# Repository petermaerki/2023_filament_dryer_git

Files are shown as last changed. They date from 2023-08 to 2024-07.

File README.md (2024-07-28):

# 2023_filament_dryer

This page is explains the physical aspects.

These topics are not covered:
* Open Hardware and Open Software...
* How to build
* User Guide
* How to run grafana etc.

## Introduction

This filament dryer is used to dry 3D printer filament.

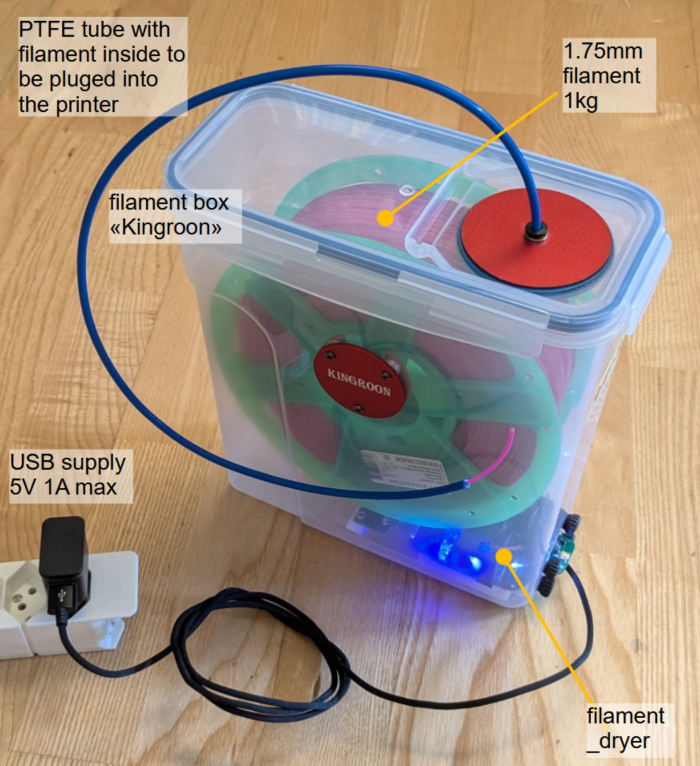
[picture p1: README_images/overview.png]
Overview


A plastic box (Aliexpress, Kingroon, USD23) is equiped with a dryer module. The module is pluged to USB power (5V, 1A max). The dryer contains about 10g of dried silicagel. A fan blows dry air around the filament. The silicagel will be automatically regenerated when saturated with water: its heated up and the wet air is blown to the enviroment.
It takes about 5 days to dry 1 kg of 1.75 mm filament.

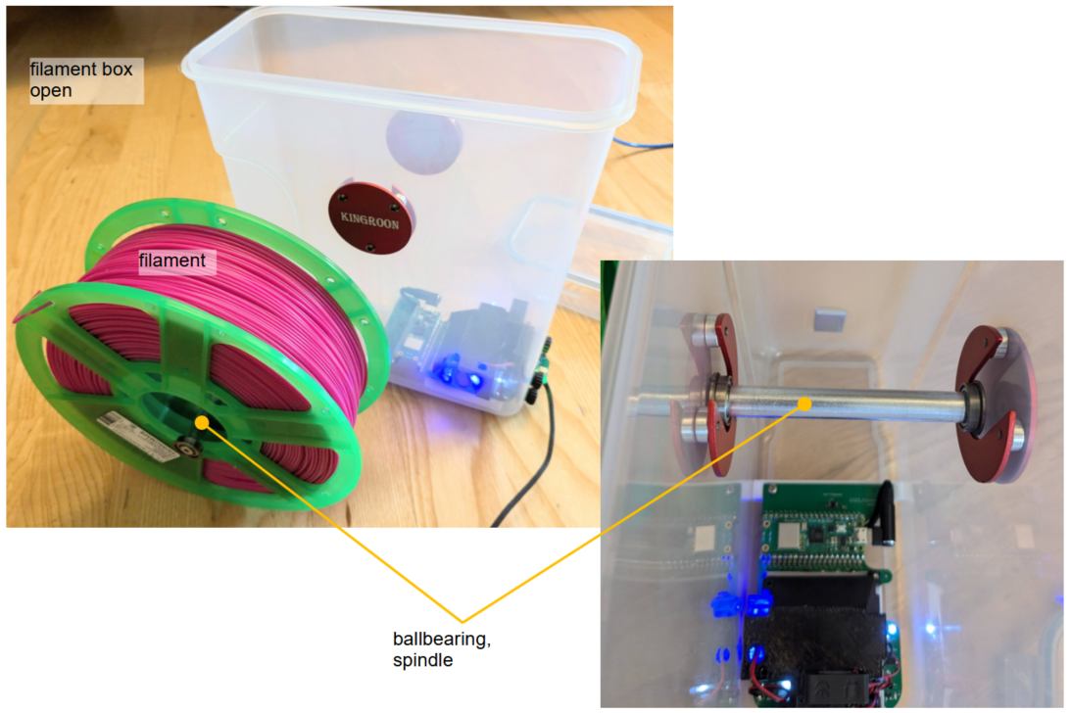
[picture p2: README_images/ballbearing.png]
Spindle


The filament roll is held by a spindle with ballbearings. 

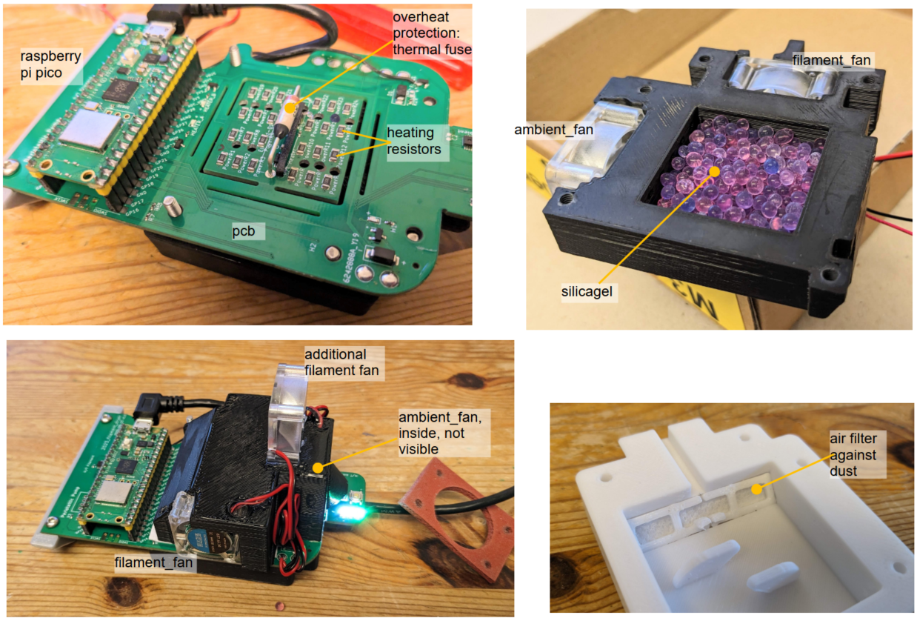
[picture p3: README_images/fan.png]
details


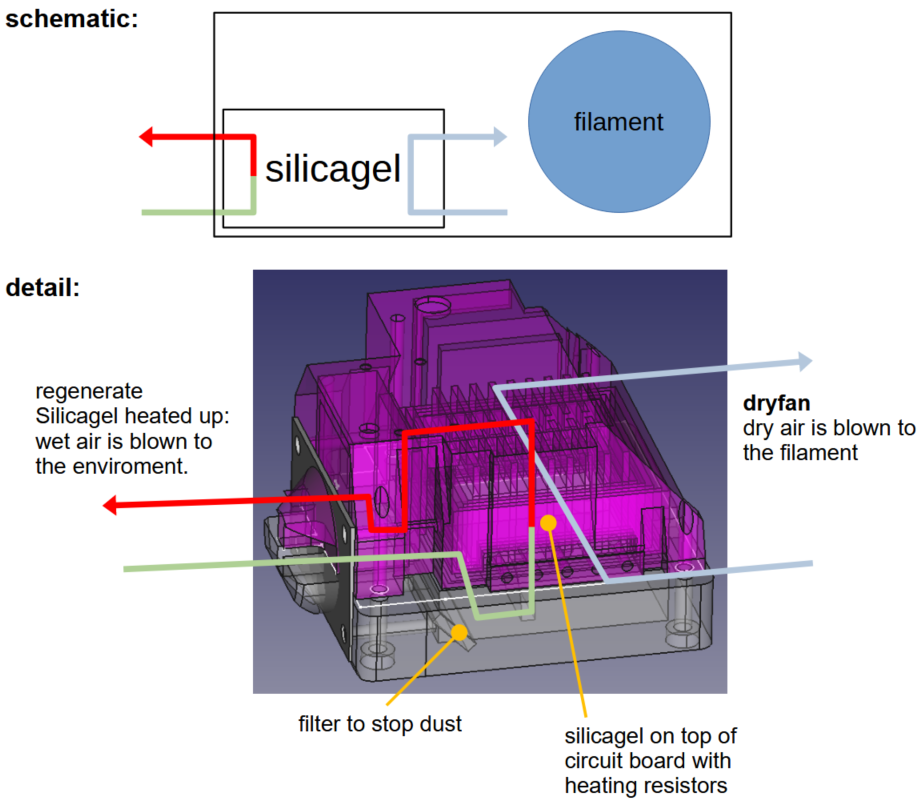
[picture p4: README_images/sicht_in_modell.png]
Airflow Model


## Drying process

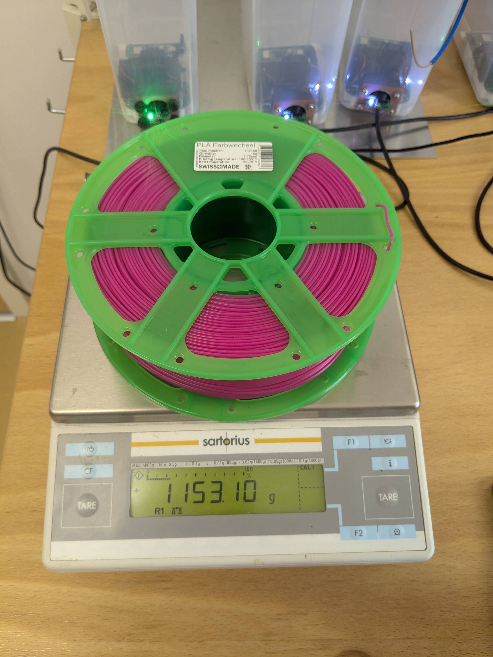
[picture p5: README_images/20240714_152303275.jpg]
Filament roll on the scale


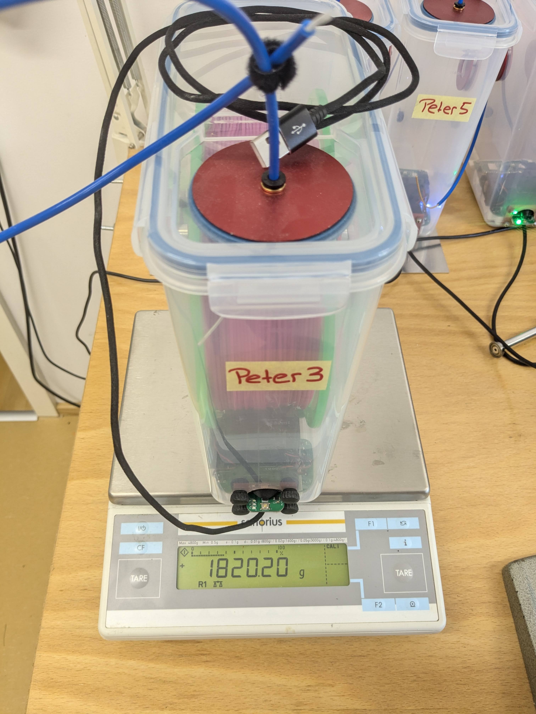
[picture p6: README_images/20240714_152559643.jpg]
Complete box an scale


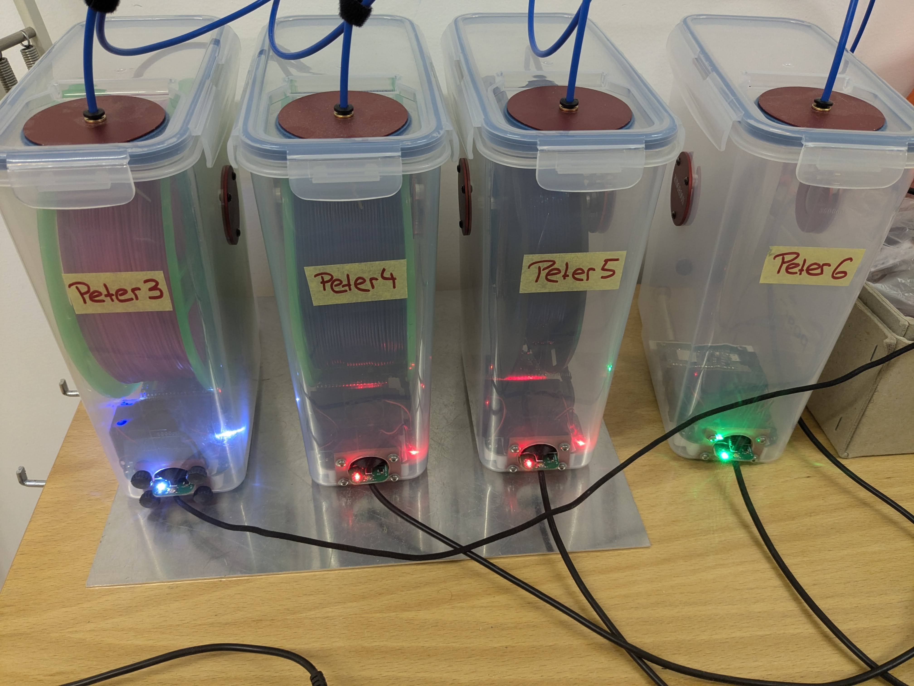
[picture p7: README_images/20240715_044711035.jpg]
Boxes


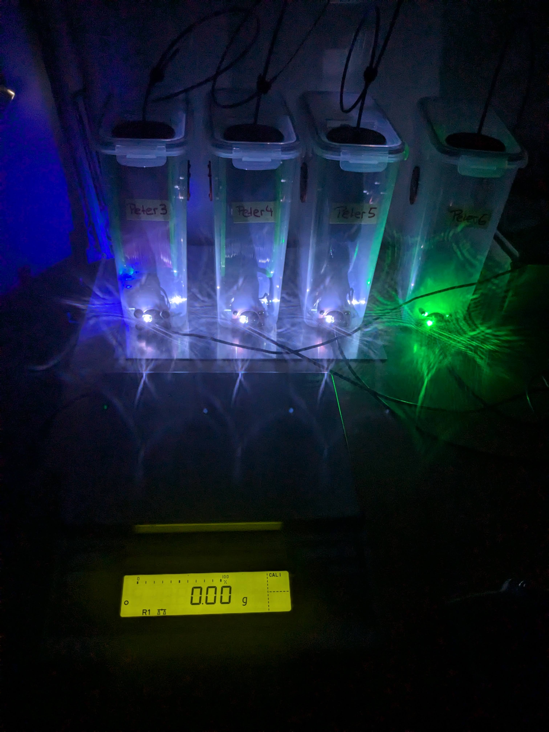
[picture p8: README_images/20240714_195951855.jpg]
Boxes in the dark


Three rolls of filament are placed in filament_dryers. PLA, PETG and TPU. The rolls have been laying around in my workshop for a long time and therefore I assume they are equally "wet". The filament_dryer is pluged in and I measure the weight of the hole dryer box over the next two weeks.
In the diagramm I show the weight reduction relative to the filament weight (1 kg for example).

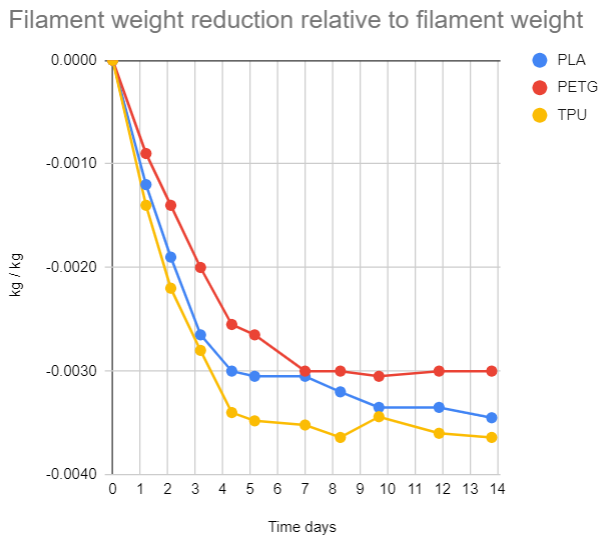
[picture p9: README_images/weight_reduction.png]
Weight loss against time


Filament types
* PLA	Pink	PLA 1.75 mm 102468 Purefil 1kg
* PETG	dunkelblau	PETG 1.75 mm 102478 Purefil 1 kg
* TPU	blau_transparent	TPU 1.75 mm LOT 20221216 Aliexpress 0.5 kg

### Conclusion

* All of the tested Filaments loose about 3 gramm water per kg filament over a week. I assume the water content after a week is low and perfect for printing.
* The fluctuation of the weight after day 6 is not a measuring error. It is due to the regeneration cycle of the dryer. Water goes into the dry box through the plastic walls or air gaps and gets out through the regenation cycle every few days.

### Drying details

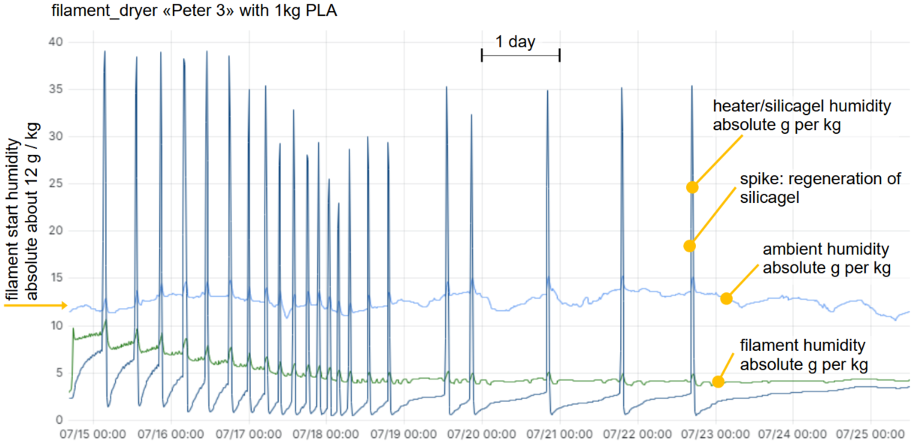
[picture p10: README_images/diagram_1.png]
Diagram two weeks absolute humidity

As an example the details of the drying over two weeks are shown.
I do show the absolute water content of the air in g per kg of air. 1 kg air corresponds to about 1 m3 air. The absolute humidity does not depend on temperature and after playing around with different himidity units for a long time, I decided to prefer this unit.

The humidity of the air around the filament changes from 12 g/kg at the start (the filament was laying around in my workshop at this himidity, ambient) to 4 g/kg after one week.

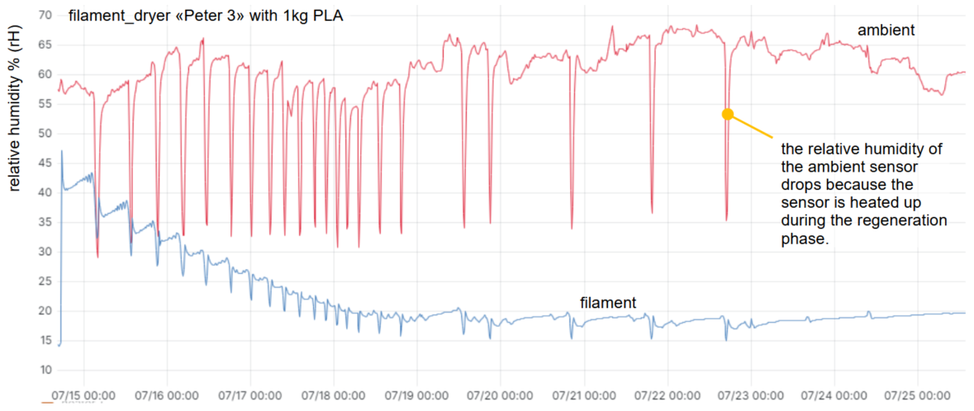
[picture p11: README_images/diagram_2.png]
Diagram two weeks relative humidity

The relative humidity in my workshop is in the range of 60%. The relative humidity of the air arount the filament is decreased down to below 20%.

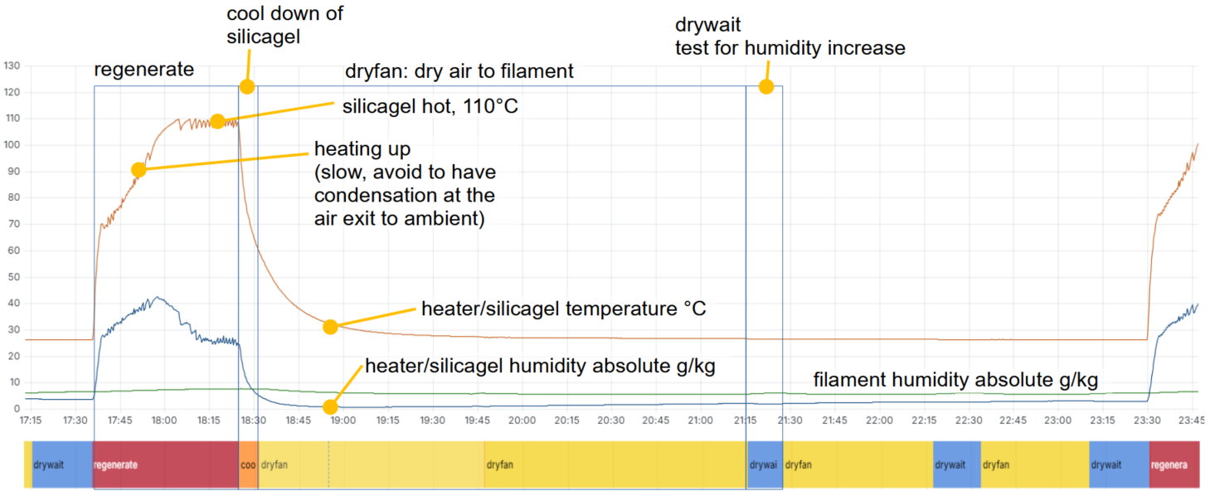
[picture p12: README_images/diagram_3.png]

One cycle of regeneration and drying.

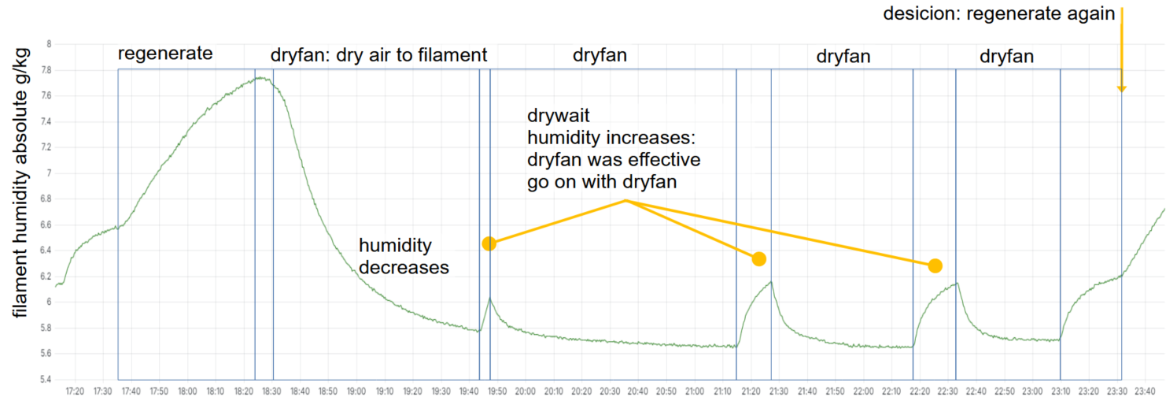
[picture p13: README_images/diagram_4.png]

The decision how to proceed is made due to changes of measurenents. If we only observe changes we are not sensitive to measurements errors/offsets. 

# Grafana
It is possible to log to grafana.
[Example](http://www.maerki.com:3000/goto/Yx-3weXSR?orgId=1)

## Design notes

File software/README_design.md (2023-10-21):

# Design decisions

## WLAN and MQTT internet connections

* At micropython boot:
  * Start watchdog
  * wlan connect
  * mqtt broker connect
  * If failed:
    * Just remember, do not try to connect/reconnect
    * Run statemachine and do not access WLAN
    * After 1h: reboot
  * If success:
    * Run statemachine and access WLAN
    * If socket error during mqtt publish:
      * Just remember, do not try to connect/reconnect
    * After 1h: reboot

## Statemachine and Watchdog

* Statemachine
  * Start in state `drywait`
  * Just before `sensors.measure()`: Reset watchdog.

# User elements

* Button long: Reboot (and reconnect to wlan)
* Button short: Next state
* LED green: state `drywait`
* LED white: state `dryfan` 
* LED red: state `regenerate/cooldown`

# WLAN in seperate thread

* No timer watchdog is required as the statemachine will feed() the wdt.

```
wdt_counter = 1
def feed():
  global wdt_counter
  if wdt_counter > 0:
     wdt_counter -= 1
  if wdt_counter == 0:
     wdt.feed()

Other core

def wlan_connect():
   wdt_counter = 10 # 10 times 8s
   wlan.connect()
   wdt_counter = 0
```
```
class SlowWdt:
  def __init__(self):
    self._start_ms: int = None
    self._expiration_ms: int = None

  def __activate__(self, expiration_ms: int):
    self._expiration_ms = expiration_ms
    self._start_ms = time.now()
  
  def feed(self):
    duration_ms = diff(time.now, self._start_ms) 
    if duration_ms > self._expiration_ms:
       reboot

def feed():
  global wdt_counter
  if wdt_counter > 0:
     wdt_counter -= 1
  if wdt_counter == 0:
     wdt.feed()

def wlan_connect():
  wdt_wlan_start_ms = time.now()
  wlan.connect()
  wdt_wlan_start_ms = None
```

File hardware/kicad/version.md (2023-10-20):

# 2023-07-16 v0.1

Manuelle Korrekturen
USB3 Muffe nach hinten verschoben
Um 90 Grad gedreht: U1, U4, U5, U6

# 2023-07-17 v0.2

Fix Footprint of R Heating
Add R for 1wire

Manuelle Korrekturen
USB3 Muffe nach hinten verschoben
Um 90 Grad gedreht: U1, U4, U5, U6

# 2023-07-18 v0.3

Final steps

* Schema Editor: File -> Page Settings: Update Revision & issue date
* Schema Editor: Inspect -> Electrical Rule Checker -> 0 Errors, 0 Warnings
* PCB Editor: File -> Page Settings: Update Revision & issue date
* PCB Editor: Tools -> Clean up tracks & vias -> check all
* PCB Editor: Inspect -> Design Rule Checker -> 0 Errors, 0 Warnings
* PCB Editor: Button "Fabrication Toolkit"

Manuelle Korrekturen in JLC
USB3 nach hinten verschoben
Um 90 Grad gedreht: U1, U4, U5, U6

# 2023-09-08 v0.6

Probleme:
 * FET Q1-Q8: Pins falsch.
 * FET Q1-Q8: Falsch: https://ngspice.sourceforge.io/docs/ngspice-manual.pdf
 * FET Q1-Q8: Korrekt: https://datasheet.lcsc.com/lcsc/1810010522_Infineon-Technologies-IRLML6244TRPBF_C143946.pdf
 * R1 4.7k: Zu gross, 2k ist ok.
 * Warum hat JLCPCB Komponenten verdreht?
 * Schrauben für Gehäuse: Sperrzone um Kurzschluss zu verhindern.
 * Schema: HT_SILICAGEL_SCA -> HT_SILICAGEL_SDA

 * Konsistente Namensgebung: SILICAGEL, FILAMENT, AMBIENT. Falsch ist BOARD, EXTs

# 2023-09-28 v1.0
  * DONE: GPIO_FAN_AMBIENT is missing!
  * DONE: HT Spare weg!
  * DONE: Ambient Sensor: C2 ist unter dem Gehäuse!
  * OK: Löcher unter Pico sind unnütz!
  * DONE: silicagel_fan -> filament_fan
  * DONE: Unterhalb Pico: Kein Kupfer wegen Antenne

# 2023-10-20 v1.1

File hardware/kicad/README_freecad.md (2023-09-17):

# FreeCAD

## PCB -> KiCad

### FreeCAD

In Python Console:

```python
objs=[]
objs.append(FreeCAD.getDocument("_0230917p_filament_dryer_silicagel").getObject("Body002"))
import importDXF
importDXF.export(objs, u"/tmp/dryer_board.dxf")

del objs
```

### KiCad

* KiCad PCB: Menu `File -> Import Graphics`
  * `/tmp/dryer_board.dxf`
  * At `0`, `0`
  * Layer `Edge.Cuts`
  * Import scale: `1`
  * `check` Group Items
  * Default line width `0.2 mm`
  * Default units: `Millimeters`

Flip horizontally!

## Footprint -> KiCad

### FreeCAD

In Python Console:

```python
objs=[]
objs.append(FreeCAD.getDocument("_0230917p_filament_dryer_silicagel").getObject("Body"))
import importDXF
importDXF.export(objs,u"/tmp/dryer_print3d.dxf")

del objs
```

In VSCode:

`mv /tmp/dryer_print3d.dxf ./hardware_kicad/Parts/dryer_print_3d`

### KiCad

Footprint Editor

* Menu `New Footprint...`
  * Name: `dryer_print3d`
  * Footprint type `Other`

* Menu `File -> Import Graphics`
  * `/tmp/dryer_print3d.dxf`
  * At `0`, `0`
  * Layer `F.Silkscreen`
  * Import scale: `1`
  * `check` Group Items
  * Default line width `0.2 mm`
  * Default units: `Millimeters`

## 3D Model -> KiCad

### FreeCAD

In Python Console:

```python
objs=[]
objs.append(FreeCAD.getDocument("_0230917p_filament_dryer_silicagel").getObject("Body"))
import ImportGui
ImportGui.export(objs,u"/tmp/dryer_print3d.step")

del objs
```

In VSCode:

`mv /tmp/dryer_print3d.step ./hardware_kicad/Parts/dryer_print_3d`

### KiCad

* Edit Footprint Properties
* Add 3D Model
* Rotation Y: `180`

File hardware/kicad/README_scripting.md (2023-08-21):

https://dev-docs.kicad.org/en/python/pcbnew/

https://github.com/mcbridejc/kicad_component_layout/blob/master/examples/led-circle/layout.py

--------------
```python

import pcbnew; print(pcbnew.PLUGIN_DIRECTORIES_SEARCH)
/usr/share/kicad/scripting
/usr/share/kicad/scripting/plugins
/home/maerki/.config/kicad/7.0/scripting
/home/maerki/.config/kicad/7.0/scripting/plugins
/home/maerki/.local/share/kicad/7.0/scripting
/home/maerki/.local/share/kicad/7.0/scripting/plugins
/home/maerki/.local/share/kicad/7.0/3rdparty/plugins

import pcbnew
ap = pcbnew.ActionPlugin()

pcb = pcbnew.GetBoard()

footprints = pcb.GetFootprints()
for footprint in footprints: print(footprint)

refdes = ""
mod = pcb.FindFootprintByReference(refdes)

footprint.GetPath().AsString()
'/85b4834f-1429-4c28-a1bb-14cdbf0ecd65'

footprint.GetDescription()
'LED SMD 1206 (3216 Metric), square (rectangular) end terminal, IPC_7351 nominal, (Body size source: http://www.tortai-tech.com/upload/download/2011102023233369053.pdf), generated with kicad-footprint-generator'

footprint.GetLayerName()
'B.Cu'

footprint.GetCenter()
VECTOR2I(192923069, 70317037)

footprint.GetReferenceAsString()
'D7'

footprint.GetReference()
'D7'

footprint.GetX()
192947000
footprint.GetY()
70292000

footprint.GetOrientationDegrees()
36.0

mod = pcb.FindFootprintByReference('D8')
mod.SetOrientationDegrees(0.0)

execfile()

```

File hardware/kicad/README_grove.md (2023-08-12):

# Grove

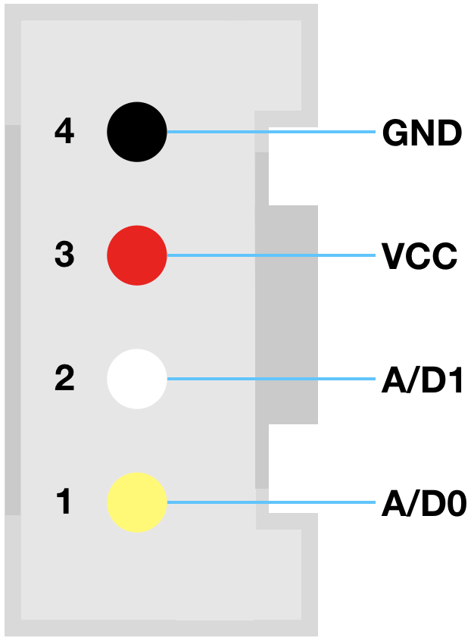
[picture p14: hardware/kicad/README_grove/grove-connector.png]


# SHT 31

| pin | color | I2C | 1-wire |
| - | :-: | - | :-: |
| pin1 | yellow | SCL | 1-wire |
| pin2 | white | SDA | - |
| pin3 | red | VCC | VCC |
| pin4 | black | GND | GND |

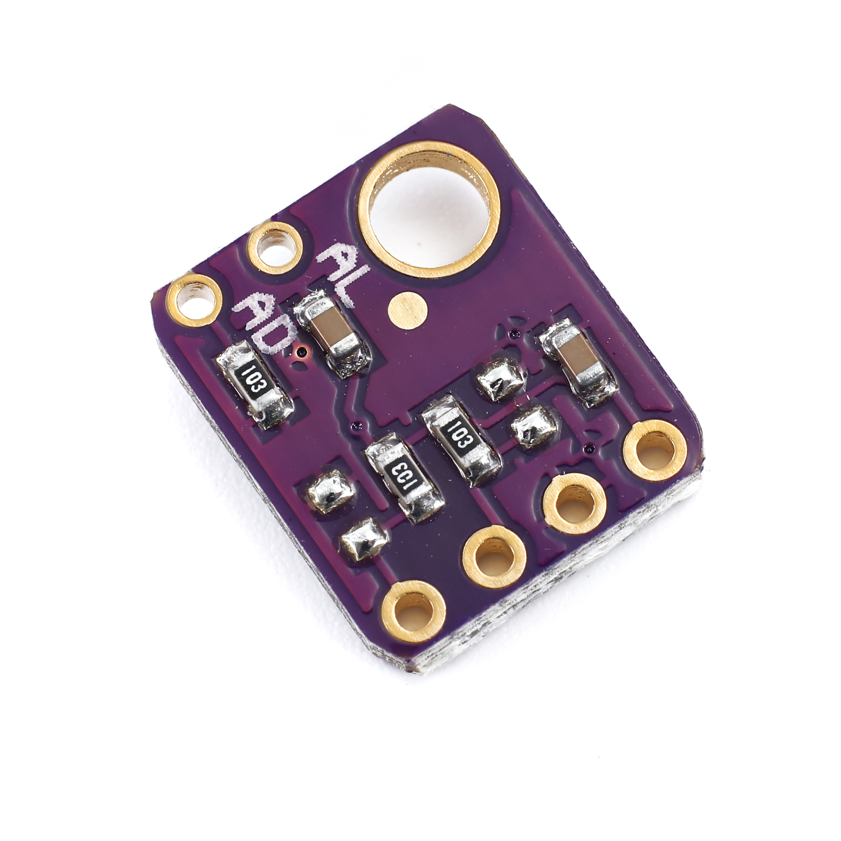
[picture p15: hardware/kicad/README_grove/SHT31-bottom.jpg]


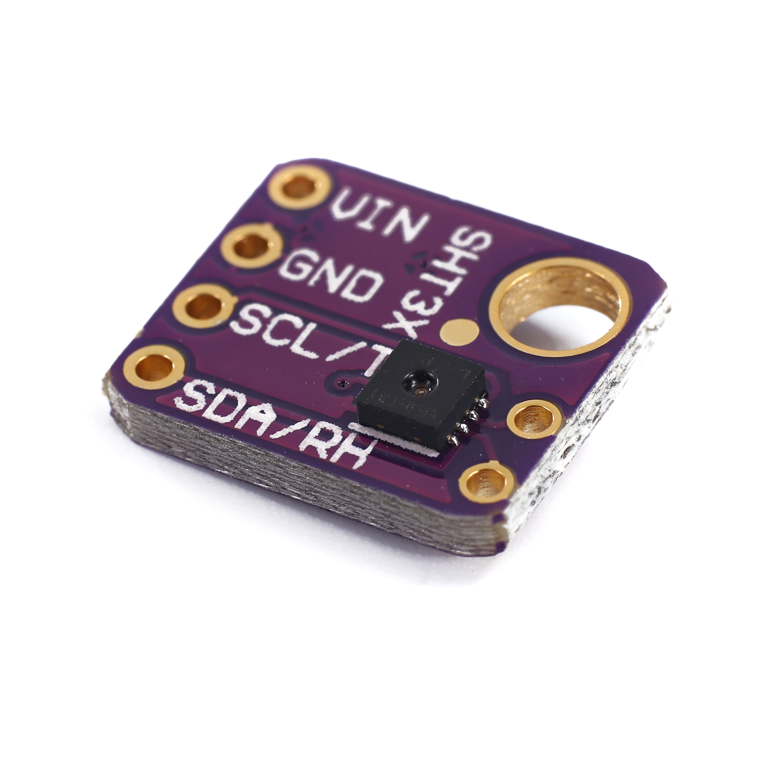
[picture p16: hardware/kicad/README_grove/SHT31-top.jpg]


# DS18b20

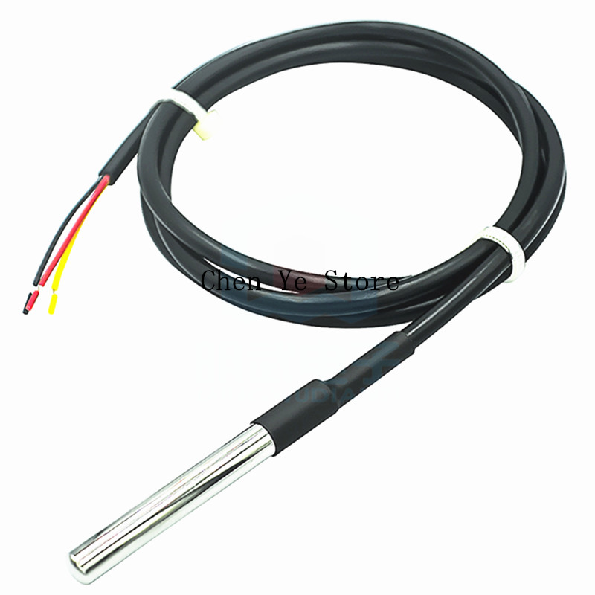
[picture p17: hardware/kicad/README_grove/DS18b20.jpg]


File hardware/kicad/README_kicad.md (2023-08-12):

# Plugins used

* https://github.com/bennymeg/JLC-Plugin-for-KiCad
  JLC PCB Plug-in for KiCad

  Fill Symbol Field `JLC Part`

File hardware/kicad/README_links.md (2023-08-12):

# Links

https://github.com/tjhorner/bizcard.git

Kicad
RP2040
Same X and Buttons

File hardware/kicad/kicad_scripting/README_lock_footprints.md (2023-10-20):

```python

import pcbnew
board = pcbnew.GetBoard()
[f.SetLocked(True) for f in board.GetFootprints() if f.GetDescription() == "SilicagelHole 1mm"]
``````

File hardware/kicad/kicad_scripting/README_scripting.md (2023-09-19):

Place files in ~/.config/kicad/7.0/scripting/plugins

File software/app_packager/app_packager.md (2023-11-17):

# App Packager

This allows a micropython device to be updated automatically over tcp.

## Workflow:
 * Commit changes to your branch
   * `.github/workflows/deploy_web_downloads.yml` will deploy all app_packages to the folder `web_downloads`
 * The micropython device will poll for changes
   * update its software

## Preparation

 * Repo: Copy `.github/workflows/deploy_web_downloads.yml`
 * Repo: Copy `software/app_packager`
 * Repo: Add `software/app_package.py`
 * Github: https://github.com/<project>/settings/pages
   * `GitHub Pages` -> `Build and deployment` -> `Source` ==> Set to `GitHub Actions`

## app_packager.py

This app will copy the files according to `app_package.py` and will deploy package.tar file to `web_downloads`.

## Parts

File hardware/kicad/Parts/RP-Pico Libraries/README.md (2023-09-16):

These files are copied from

https://github.com/ncarandini/KiCad-RP-Pico

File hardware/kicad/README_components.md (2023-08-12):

# Components

## Temperature Sensor

Grove Connector
https://wiki.seeedstudio.com/One-Wire-Temperature-Sensor-DS18B20/

Seeed KiCad Components

https://github.com/Seeed-Studio/OPL_Kicad_Library

MOUSER 713-114020164 114020164 JLC C604849 horiz No holes
MOUSER 713-114020163 114020163 JLC C604850 horiz Holes
MOUSER 713-110990030 110990030 JLC C403774 vert Holes

# Connectors - Groove

https://wiki.seeedstudio.com/Grove_System/
https://www.seeedstudio.com/Grove-Universal-4-pin-connector.html

pin	Function	Note
pin1	SCL	I2C Clock
pin2	SDA	I2C Data
pin3	VCC	Power for Grove Module, 5V/3.3V
pin4	GND	Ground

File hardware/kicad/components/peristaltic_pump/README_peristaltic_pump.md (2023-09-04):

# Peristaltic Pump

## Base Board - Aliexpress

42 Stepper Motor Driver Expansion Board DRV8825 A4988 3D Printer Control Shield Module For Arduino UNO R3 Ramps1.4 DIY Kit One

Feature:
 
On-board DIP switch, you can easily adjust the drive segments
Terminal power connector for easy connection drive power
Compatible with 12 / 24V drive scheme
Suitable for 42 stepper motor drive, 3D printers and DIY
 
Specification:
 
Size: 42 x 42 x 15mm
Fixed: 3mm
Pitch: 1400 x 1400mil (35.56 x 35.56mm)
Logic voltage: 5V
Input voltage: 12-30V
Ports: Digital
Interface: Direction, enable, speed
Applicable module: DRV8825 (not A4988)

Brand Name: MINGYUANDINGYE

## Driver Board

https://www.ti.com/lit/ds/symlink/drv8825.pdf

https://www.pololu.com/product/2133
  Current limiting

Digitec: https://www.digitec.ch/de/s1/product/purecrea-drv8825-schrittmotor-treiber-stepper-driver-modul-entwicklungsboard-kit-25442322

Other: https://techmaze.romman.store/product/99188778
Schematics: https://docs.google.com/document/d/e/2PACX-1vTyiIMFXQ1cY5TMhOh_0EjdznmC3Nw6CplW7Xx8F61ogOaUpHVyuaXsqrWhIiuE8SjpbON_VzB-rk3R/pub

Ohter: https://lastminuteengineers.com/drv8825-stepper-motor-driver-arduino-tutorial/

https://www.youtube.com/watch?v=AfDqchJLPxU

## Software - Driver

https://gitlab.com/robhamerling/micropython-drv8825

https://how2electronics.com/control-stepper-motor-with-drv8825-raspberry-pi-pico/

https://youtu.be/aVaOmtFGesI?si=sICGaq134060ogrd
Running Stepper Motors with MicroPython and an ESP32 - Tutorial - Software Included!
Clayton Darwin
https://gitlab.com/duder1966/youtube-projects

# Commissioning

* Grove cable to filament board
* Connection EN - GND
* MS1, MS2, MS3: 1  (1/16 step)

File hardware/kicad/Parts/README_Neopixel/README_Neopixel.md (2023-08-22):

# Neopixel

* Pro: Cool
* Con: Requires `PCBA Type: Standard`. Economic is about USD30 less per order
* Con: Neopixel more expensive (USD2.2 + USD)
* Con: Neopixel may break
* Con: Neopixel may get less hot

## Size on PCB

30mm * 30mm = 900mm2

## JLCPCB C527089

* WS2812
  * https://www.instructables.com/
  * 8X8-RGB-Neo-Pixel-Matrix-Using-JLCPCB-SMT-Assembly/
    Neopixel, WS2812

## JLCPCB C527089
* https://www.youtube.com/watch?v=MFv8F5oAv4I
  * https://www.hackster.io/sainisagar7294/8x8-rgb-neo-pixel-matrix-using-jlcpcb-smt-assembly-194697
  * https://drive.google.com/drive/folders/1tW2Useefe7okH0qp94tDFMnx26wZcE1y
    C527089
  * https://jlcpcb.com/partdetail/Worldsemi-WS2812B_BT/C2761795
    USD 0.09
    12mA -> 0.18W -> 27 Stück
  * https://jlcpcb.com/partdetail/Worldsemi-WS2812B_XF02W/C4154882

## WS2812

* https://www.hackster.io/Arnov_Sharma_makes/ws2812b-rgb-led-in-circuits-7cb39e

## JLCPCB C4154879 - WS2815E

* People reported to work rp and micropython

Pro
 *

Con
 * No standard footprint
 * 12V !!!

### Resources

[Schematic](https://www.gree-leds.com/ws-series-ic-embedded-led/12v-individually-addressable-ws2815-led.html)

[Footprint](https://www.snapeda.com/parts/WS2815/Normand/view-part/)

## JLCPCB C4154882 - WS2812

Schematic: hardware_kicad/Parts/README_Neopixel/8x8 RGB neopixel/Schematic_8X8 NEOPIXLE_2021-12-14.pdf

Footprint: Standard KiCAD

## Evaluation Neopixel

| JLCPCB | Name | Package | USD 50+ | mm2 (pieces in 900mm2) | Current | VCC |
| - | - | - | - | - | - | - |
| **SELECTED** C965555 | WS2812B-2020 Worldsemi | SMD,2x2mm | 0.078 | 4 (225) | 12mA | 5V |
| C527089 | WS2812B-Mini Worldsemi | SMD3535 | 0.085 (75) | 12 (70) | 5V |
| C4154882 | Worldsemi | SMD5050 | 0.039 | 25 (36) | 5V |
| C4154879 | WS2815E Worldsemi | SMD,5x5.4mm | 0.058 | 27 (33) | 12mA | 12V !!! |

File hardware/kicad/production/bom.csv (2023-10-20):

Designator | Footprint | Quantity | Value | LCSC Part #
C1, C2, C20 | 0603 | 3 | 10u | C96446
D1, D11, D2 | D_SMA | 3 | General Purpose Diode | C95872
D10, D7 | 0603 | 2 | WHITE | C2290
D3 | 0603 | 1 | HEATER_A | C2286
D4 | 0603 | 1 | HEATER_B | C2286
D5 | 0603 | 1 | W | C2290
D6 | 0603 | 1 | RED | C2286
D8 | 0603 | 1 | R | C2286
D9 | 0603 | 1 | G | C2297
FanQ1, FanQ2, FanQ3, PowerQ1, PowerQ2 | SOT-23 | 5 | NMOS | C143946
H1, H2, H3, H4, H5 | MountingHole_3.2mm_M3 | 5 | MountingHole
PowerR1, PowerR10, PowerR11, PowerR12, PowerR13, PowerR14, PowerR15, PowerR16, PowerR17, PowerR18, PowerR19, PowerR2, PowerR20, PowerR21, PowerR22, PowerR23, PowerR24, PowerR3, PowerR4, PowerR5, PowerR6, PowerR7, PowerR8, PowerR9 | 1206 | 24 | 120 | C17909
R1, R10, R11, R19, R2, R20, R6, R9 | 0402 | 8 | 470R
R4, R5, R7, R8 | 0402 | 4 | 10k
TP1 | TestPoint_Pad_D3.0mm | 1 | B+
TP10 | TestPoint_Pad_D3.0mm | 1 | S-
TP2 | TestPoint_Pad_D3.0mm | 1 | B-
TP7 | TestPoint_Pad_D3.0mm | 1 | A+
TP8 | TestPoint_Pad_D3.0mm | 1 | A-
TP9 | TestPoint_Pad_D3.0mm | 1 | S+
U1 | SON50P250X250X90-9T110X180N | 1 | H/T Filament | C80862
U2 | SON50P250X250X90-9T110X180N | 1 | H/T Heater | C80862
U3 | SON50P250X250X90-9T110X180N | 1 | H/T Ambient | C80862
USER_BUTTON1 | SW_TS-1187A-B-A-B | 1 | USER | C318884

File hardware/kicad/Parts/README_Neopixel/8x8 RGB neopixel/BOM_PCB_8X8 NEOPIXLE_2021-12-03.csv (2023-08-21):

ID | Name | Designator | Footprint | Quantity | Manufacturer Part | Manufacturer | Supplier | Supplier Part | Price
1 | PH-00014 | H1,H2 | HDR-TH_3P-P2.54-V-M | 2 | PH-00014 | Liansheng(连盛) | LCSC | C2685130 | 0.015
2 | WS2812B-MINI | LED1,LED2,LED3,LED4,LED5,LED6,LED7,LED8,LED9,LED10,LED11,LED12,LED13,LED14,LED15,LED16,LED17,LED18,LED19,LED20,LED21,LED22,LED23,LED24,LED25,LED26,LED27,LED28,LED29,LED30,LED31,LED32,LED33,LED34,LED35,LED36,LED37,LED38,LED39,LED40,LED41,LED42,LED43,LED44,LED45,LED46,LED47,LED48,LED49,LED50,LED51,LED52,LED53,LED54,LED55,LED56,LED57,LED58,LED59,LED60,LED61,LED62,LED63,LED64 | LED-SMD_4P-L3.5-W3.5-TL_WS2812B | 64 | WS2812B-Mini | Worldsemi | LCSC | C527089 | 0.107

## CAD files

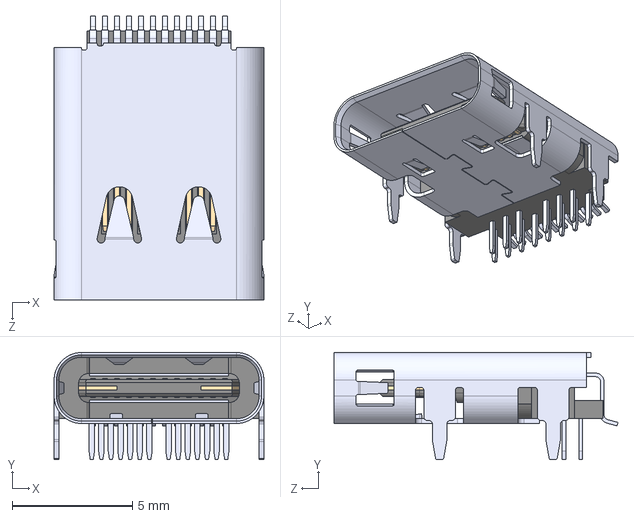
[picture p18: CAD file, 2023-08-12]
hardware/kicad/Parts/bizcard/footprints/SS-52400-002--3DModel-STEP-56544.STEP
8.74 x 4.46 x 11.8 mm

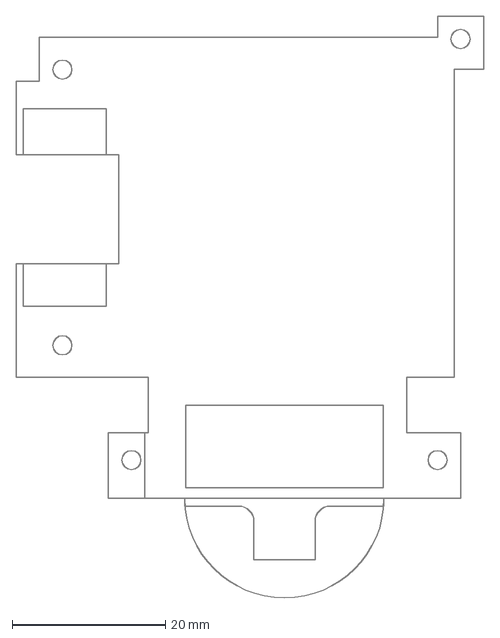
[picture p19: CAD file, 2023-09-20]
hardware/kicad/Parts/dryer_print_3d/dryer_print3d_cleaned.dxf
61.0 x 76.0 mm

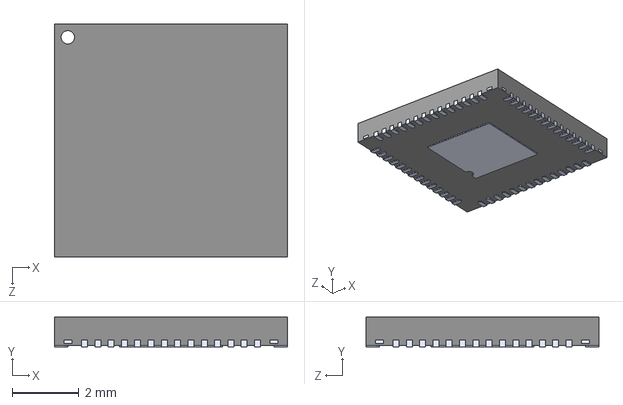
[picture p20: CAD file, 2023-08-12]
hardware/kicad/Parts/snapeda/RP2040/RP2040.step
7.00 x 0.9 x 7.00 mm

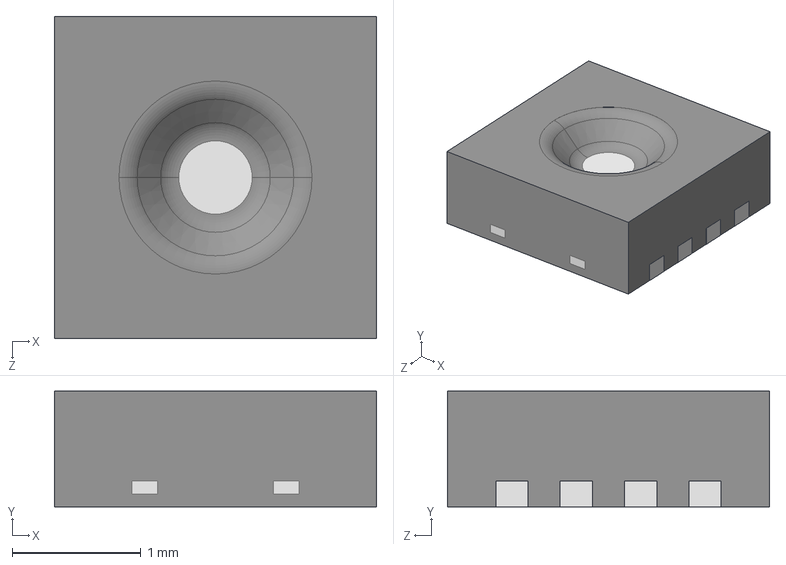
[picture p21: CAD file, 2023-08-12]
hardware/kicad/Parts/snapeda/SHT31/SHT31.step
2.50 x 0.901 x 2.50 mm

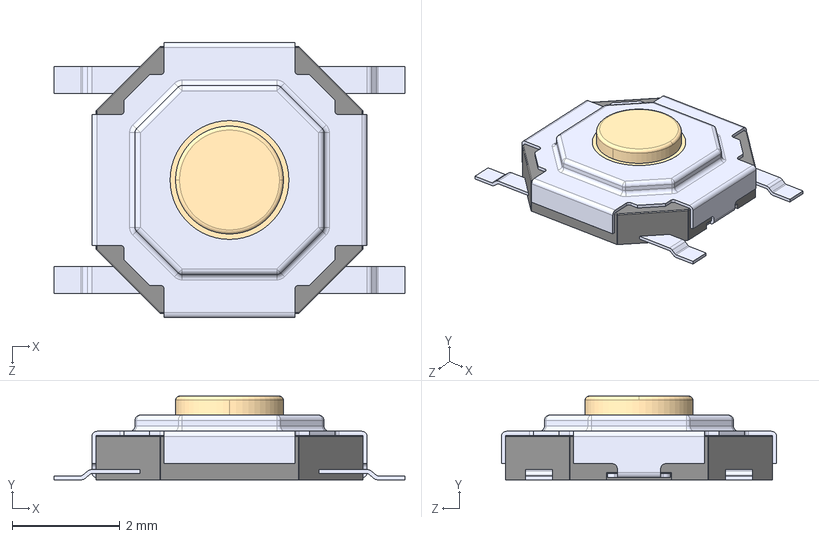
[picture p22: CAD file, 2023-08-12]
hardware/kicad/Parts/snapeda/TS-1187A-B-A-B/TS-1187A-B-A-B.step
6.50 x 1.55 x 5.10 mm

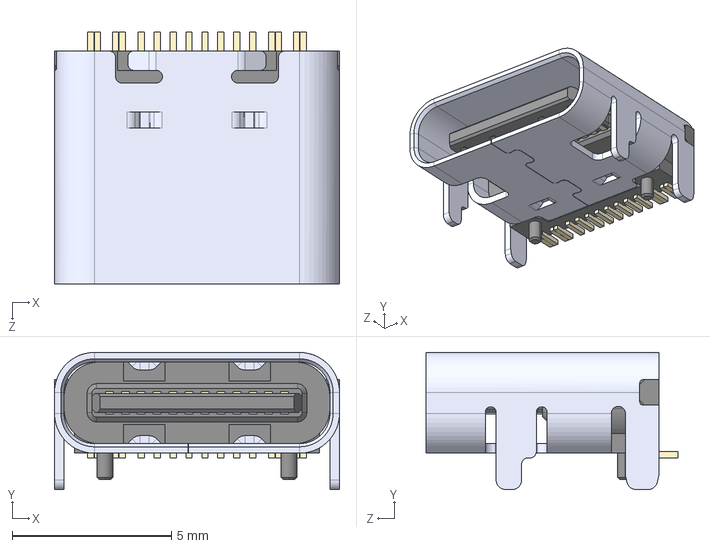
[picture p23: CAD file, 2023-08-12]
hardware/kicad/Parts/snapeda/TYPE-C-31-M-12/TYPE-C-31-M-12.step
8.94 x 4.30 x 7.90 mm

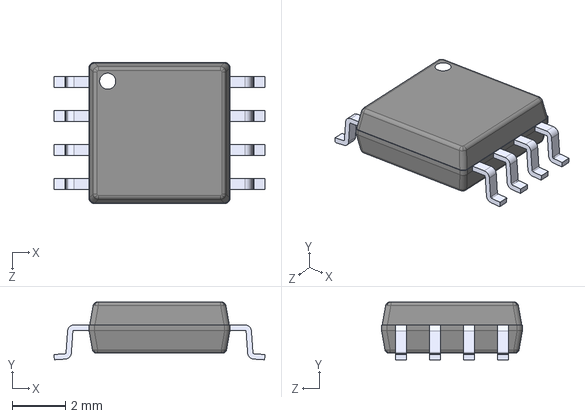
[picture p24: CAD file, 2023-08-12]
hardware/kicad/Parts/snapeda/W25Q128JVSIQ/W25Q128JVSIQ.step
7.90 x 2.16 x 5.28 mm

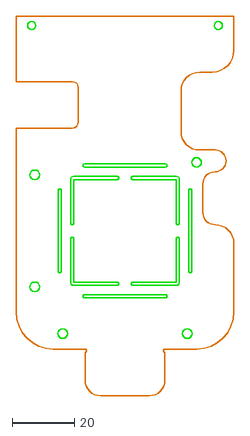
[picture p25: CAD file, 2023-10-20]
hardware/kicad/print3d_freecad/dryer_board_fixed_cleaned.dxf
70.0 x 122.0

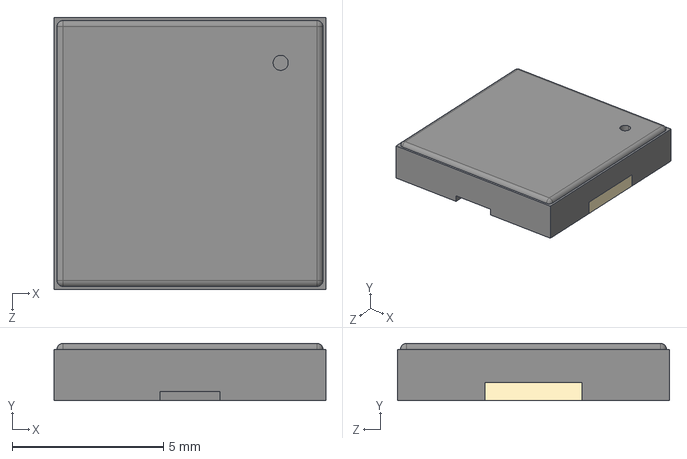
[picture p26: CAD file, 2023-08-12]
hardware/kicad/Parts/bizcard/footprints/PKMCS0909E4000-R1--3DModel-STEP-56544.STEP
9.00 x 1.90 x 9.00 mm

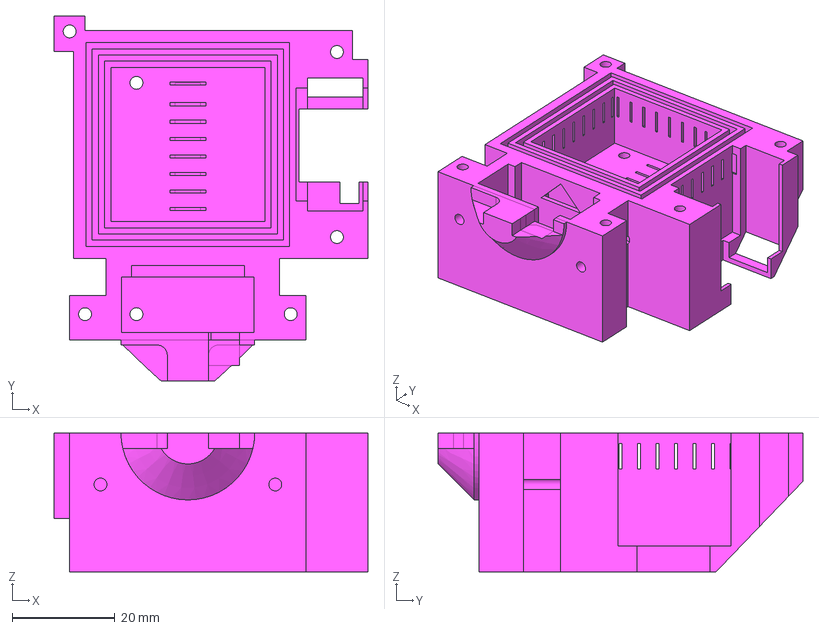
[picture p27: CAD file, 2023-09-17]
hardware/kicad/Parts/dryer_print_3d/dryer_print3d.step
61.0 x 71.0 x 27.0 mm

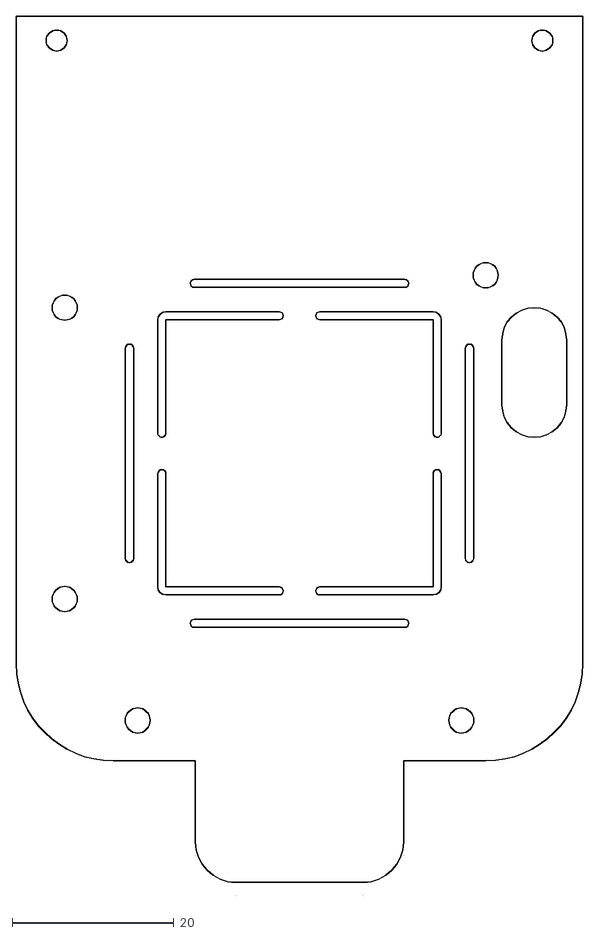
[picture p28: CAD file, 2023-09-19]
hardware/kicad/print3d_freecad/dryer_board_fixed.dxf
70.0 x 108.7

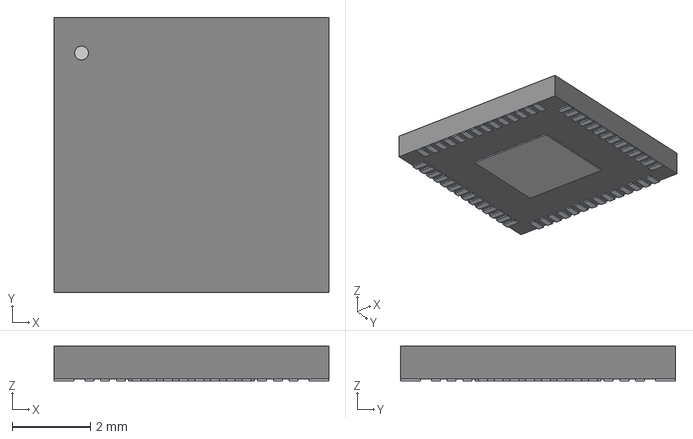
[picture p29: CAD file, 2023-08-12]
hardware/kicad/Parts/bizcard/footprints/IC57_RP2040.step
7.01 x 7.01 x 0.892 mm

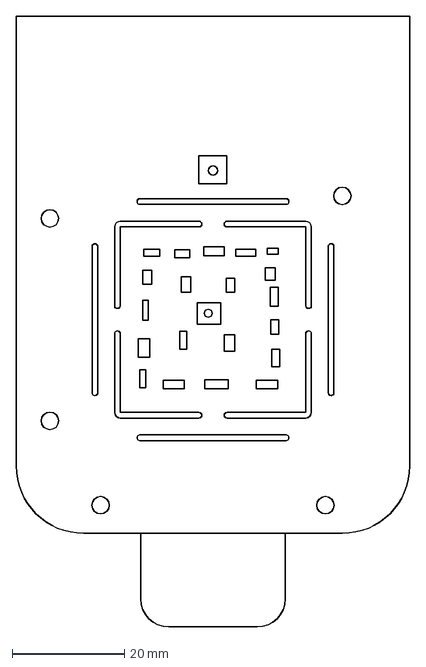
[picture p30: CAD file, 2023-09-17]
hardware/kicad/print3d_freecad/dryer_board.dxf
70.0 x 108.7 mm

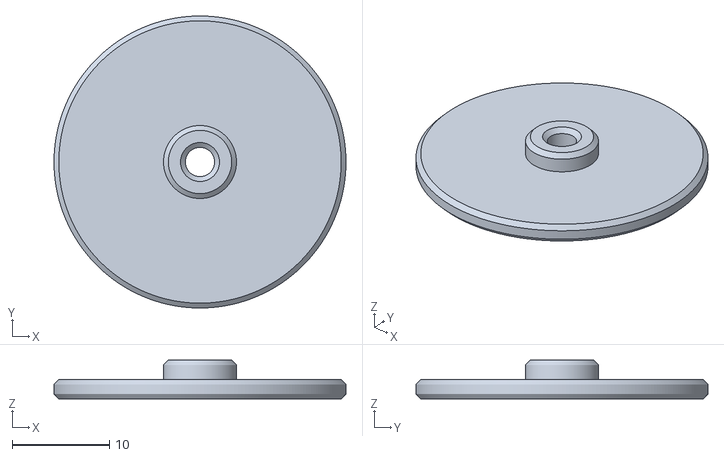
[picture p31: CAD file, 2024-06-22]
hardware/freecad/20231102a_ptfe_schlauch_anschlag-scheibe_oben.stl
30.0 x 30.0 x 4.00

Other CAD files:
hardware/kicad/Parts/mouser/LIB_110990030/110990030/3D/110990030.stp
hardware/kicad/Parts/mouser/LIB_114020164/114020164/3D/114020164.stp
hardware/freecad/20240619a_filament_dryer_silicagel-filterpapierklemmer_PETG.stl
hardware/freecad/20231102a_ptfe_schlauch_anschlag-seitlich.stl
hardware/freecad/20231102a_ptfe_schlauch_anschlag.FCStd
hardware/freecad/20240619a_filament_dryer_silicagel-barriere_PETG.stl
hardware/freecad/20240619a_filament_dryer_silicagel-filterpapierklemmer_mirrored PETG.stl
hardware/freecad/20240619a_filament_dryer_silicagel-teil_oben_ASA.stl
hardware/freecad/20240619a_filament_dryer_silicagel-teil_unten_PETG.stl
hardware/kicad/Parts/dryer_print_3d/dryer_print3d.dxf
hardware/kicad/print3d_freecad/20230917p_filament_dryer_silicagel.FCStd

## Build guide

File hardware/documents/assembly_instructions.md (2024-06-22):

# Assembly instructions
## Circuit Board
Raspberry Pi Pico W mit MicroPython v1.21.0

* Ordner `software\micropython`: `config_secrets.py` auspacken/ausfüllen. In Thonny, `config_secrets.py` auf das Filesystem kopieren.
* In VSCode Debug: `run_from_pc`: Dies kopiert alle Files auf den pico.
* Jetzt starten der pico und wird als erstes mit dem Wlan verbinden und die aktuelle Version aus dem Web herunterladen.

* Um mit `run_from_pc` debuggen zu können, `False` eintragen bei:
```python
main.py
ENABLE_APP_PACKAGE_UPDATE = True
ENABLE_WDT = True
```

Buchsenleisten und Stiftenleisten fuer RP Pico W  
Micro USB Kabel

Thermal Fuse D139-002 (141C), soldered 7 mm above circuit board surface. See Picture.

3D Prints:
* 20240619a_filament_dryer_silicagel-teil_oben_ASA
* 20240619a_filament_dryer_silicagel-teil_unten_PETG
* 20240619a_filament_dryer_silicagel-barriere_PETG
* 20240619a_filament_dryer_silicagel-filterpapierklemmer_PETG
* 20240619a_filament_dryer_silicagel-filterpapierklemmer_mirrored_PETG

Filterpapier  
20231027_filterpapier_abmessung.txt

EVA Foam, 2 mm thick, cut to size:  
20231028_schneidelehre.pdf

EVA Foam 3mm, cut to size, to make it tight against the plastic casing.
20231028_schneidelehre.pdf

Fans
```
2 (or 3 piece)
Fan 2510 (25 mm x 25 mm x 10 mm) 5V slow running fan, 2 pin cable.
Cheap from aliexpress or
Distrelec 301-48-121  MF25100V2-1000U-A99
```

Screws
* 5   M3x20 Linsenkopf (oberes und unteres Teil)
* 2   M3x8 Linsenkopf (Balken)
* 4   M3x10 Linsenkopf (für die Montage in der Plastikbox)

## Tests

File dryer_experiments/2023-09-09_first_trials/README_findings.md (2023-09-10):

** Filesystem size

* Filenamen dryer jlcpcb: 8 MBytes
* Raspberry Pi Pico: 2 MBytes

* 2023-09-10a_logdata.txt -> 842_681Bytes
* Log every 2 seconds
* Duration: 18_798_791ms -> 5.22h
* Disk size: 1.4MBytes
* Max duration: 5.22h * 1.4MBytes / 842_681Bytes = 5.22*1_400_000/842_681 = 8.6h

* 10s statt 2s -> 43h statt 8.6h

** How to run a test

* VSCode: `run_from_pc`
* Prepare / format filesystem: Micropython: `rf()`
* VSCode: `run_from_pc`
* Let experiment run
* Check 'disk free': Micropython: `df()`
* Stop experiment: Micropython: `stop()`

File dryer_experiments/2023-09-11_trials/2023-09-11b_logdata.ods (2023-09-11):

78 | SENSORS_HEADER | heater_heater | silicagel_Fan | ambient_Fan | silicagel_C | silicagel_rH | silicagel_dew | board_C | board_rH | board_dew | ext_C | ext_rH | ext_dew | heater_C | aux_C
80 | SM_STATE | 'none' -> 'regenerate' Statemachine initialization
877 | SENSORS_VALUES | 78 | 0 | 0 | 29.67 | 25.2 | 7.7 | 26.87 | 16.4 | -0.7 | 24.6 | 57.8 | 15.8 | 74.81 | 24.81
10792 | SENSORS_VALUES | 78 | 0 | 0 | 29.82 | 25.8 | 8.1 | 26.93 | 16.4 | -0.6 | 24.58 | 57.9 | 15.8 | 75.31 | 24.88
11692 | SM_STATE | 'regenerate' -> 'dryfan' Manual intervention
20780 | LOG_INFO | len=0, append(-0.4041748)
20794 | SENSORS_VALUES | 0 | 1 | 0 | 30.01 | 25.5 | 8.1 | 26.94 | 16.7 | -0.4 | 24.6 | 57.7 | 15.8 | 74.5 | 24.81
30791 | SENSORS_VALUES | 0 | 1 | 0 | 30.15 | 26.5 | 8.8 | 26.97 | 17.3 | 0.1 | 24.59 | 57.7 | 15.7 | 71.38 | 24.88
40791 | SENSORS_VALUES | 0 | 1 | 0 | 30.32 | 27.3 | 9.4 | 26.94 | 17.9 | 0.5 | 24.62 | 57.6 | 15.7 | 67.75 | 24.88
50791 | SENSORS_VALUES | 0 | 1 | 0 | 30.48 | 27.9 | 9.9 | 26.97 | 18.3 | 0.9 | 24.6 | 57.5 | 15.7 | 64.38 | 24.88
60792 | SENSORS_VALUES | 0 | 1 | 0 | 30.66 | 28.4 | 10.3 | 26.93 | 18.7 | 1.2 | 24.62 | 57.5 | 15.7 | 61.38 | 24.88
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

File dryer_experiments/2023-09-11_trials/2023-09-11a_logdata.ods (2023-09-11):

125 | SENSORS_HEADER | heater_heater | silicagel_Fan | ambient_Fan | silicagel_C | silicagel_rH | silicagel_dew | board_C | board_rH | board_dew | ext_C | ext_rH | ext_dew | heater_C | aux_C
127 | SM_STATE | 'none' -> 'regenerate' Statemachine initialization
924 | SENSORS_VALUES | 78 | 0 | 0 | 30.93 | 20.4 | 5.6 | 27.45 | 46.5 | 15 | 25.92 | 62.4 | 18.2 | 80.31 | 25.81
10793 | SENSORS_VALUES | 78 | 0 | 0 | 31.24 | 20.6 | 6.1 | 27.54 | 46.4 | 15 | 25.91 | 62.4 | 18.2 | 79.63 | 25.81
20792 | SENSORS_VALUES | 78 | 0 | 0 | 31.49 | 20.8 | 6.4 | 27.58 | 46.3 | 15.1 | 25.95 | 62.4 | 18.3 | 80.75 | 25.81
30792 | SENSORS_VALUES | 78 | 0 | 0 | 31.79 | 21.1 | 6.8 | 27.65 | 46.2 | 15.1 | 25.95 | 62.4 | 18.3 | 81.88 | 25.94
40793 | SENSORS_VALUES | 78 | 0 | 0 | 32.07 | 21.3 | 7.3 | 27.72 | 46.1 | 15.1 | 25.96 | 62.4 | 18.3 | 82.88 | 25.88
50792 | SENSORS_VALUES | 78 | 0 | 0 | 32.37 | 21.5 | 7.6 | 27.78 | 46.1 | 15.2 | 26.01 | 62.2 | 18.2 | 83.88 | 25.94
60793 | SENSORS_VALUES | 78 | 0 | 0 | 32.67 | 21.7 | 8 | 27.85 | 46 | 15.2 | 26.02 | 62.2 | 18.3 | 84.75 | 25.94
70791 | SENSORS_VALUES | 78 | 0 | 0 | 32.94 | 22 | 8.4 | 27.91 | 45.9 | 15.2 | 26.04 | 62 | 18.2 | 85.44 | 25.94
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

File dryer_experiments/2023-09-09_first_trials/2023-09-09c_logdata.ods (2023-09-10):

 |  | heater_heater | silicagel_Fan | ambient_Fan | silicagel_C | silicagel_rH | silicagel_dew | board_C | board_rH | board_dew | ext_C | ext_rH | ext_dew | heater_C | aux_C
330801 | SENSORS_VALUES | 200 | 0 | 1 | 39.6 | 49.1 | 27 | 29.77 | 61.7 | 21.7 | 25.98 | 65.9 | 19.1 | 89.13 | 27.38
332801 | SENSORS_VALUES | 200 | 0 | 1 | 39.63 | 49.1 | 27 | 29.79 | 61.7 | 21.7 | 25.99 | 65.8 | 19.1 | 89.19 | 27.38
334801 | SENSORS_VALUES | 200 | 0 | 1 | 39.65 | 49.2 | 27 | 29.77 | 61.7 | 21.7 | 25.99 | 65.7 | 19.1 | 89.25 | 27.38
336805 | SENSORS_VALUES | 200 | 0 | 1 | 39.63 | 49.2 | 27 | 29.76 | 61.7 | 21.7 | 26.01 | 65.6 | 19.1 | 89.25 | 27.38
338801 | SENSORS_VALUES | 200 | 0 | 1 | 39.69 | 49.2 | 27.1 | 29.76 | 61.7 | 21.7 | 26.01 | 65.6 | 19.1 | 89.31 | 27.38
340801 | SENSORS_VALUES | 200 | 0 | 1 | 39.67 | 49.3 | 27.1 | 29.8 | 61.7 | 21.7 | 25.99 | 65.8 | 19.1 | 89.38 | 27.38
342801 | SENSORS_VALUES | 200 | 0 | 1 | 39.69 | 49.3 | 27.1 | 29.79 | 61.7 | 21.7 | 26.01 | 65.8 | 19.2 | 89.38 | 27.38
344801 | SENSORS_VALUES | 200 | 0 | 1 | 39.7 | 49.3 | 27.1 | 29.8 | 61.7 | 21.7 | 25.99 | 66 | 19.2 | 89.44 | 27.38
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

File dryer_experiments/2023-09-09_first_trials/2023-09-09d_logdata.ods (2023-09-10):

 |  | heater_heater | silicagel_Fan | ambient_Fan | silicagel_C | silicagel_rH | silicagel_dew | board_C | board_rH | board_dew | ext_C | ext_rH | ext_dew | heater_C | aux_C
169 | SENSORS_HEADER | heater_heater | silicagel_Fan | ambient_Fan | silicagel_C | silicagel_rH | silicagel_dew | board_C | board_rH | board_dew | ext_C | ext_rH | ext_dew | heater_C | aux_C
977 | SENSORS_VALUES | 78.431374 | 0 | 1 | 35.13 | 44.5 | 21.3 | 28.81 | 49.5 | 17.2 | 25.96 | 66.5 | 19.3 | 68.88 | 27.06
2801 | SENSORS_VALUES | 78.431374 | 0 | 1 | 35.26 | 44.4 | 21.4 | 28.8 | 49.5 | 17.2 | 25.95 | 66.7 | 19.3 | 68.5 | 27.06
4801 | SENSORS_VALUES | 78.431374 | 0 | 1 | 35.45 | 44.1 | 21.4 | 28.81 | 49.5 | 17.2 | 25.96 | 66.8 | 19.3 | 68.31 | 27.06
6802 | SENSORS_VALUES | 78.431374 | 0 | 1 | 35.56 | 43.9 | 21.4 | 28.81 | 49.5 | 17.2 | 25.96 | 66.5 | 19.3 | 68.31 | 27
8801 | SENSORS_VALUES | 78.431374 | 0 | 1 | 35.61 | 43.8 | 21.4 | 28.84 | 49.5 | 17.3 | 25.98 | 66.2 | 19.2 | 68.44 | 27.06
10801 | SENSORS_VALUES | 78.431374 | 0 | 1 | 35.67 | 43.7 | 21.4 | 28.81 | 49.5 | 17.2 | 25.96 | 66.1 | 19.2 | 68.56 | 27.06
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

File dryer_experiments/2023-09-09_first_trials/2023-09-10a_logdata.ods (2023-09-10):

73 | SENSORS_HEADER | heater_heater | silicagel_Fan | ambient_Fan | silicagel_C | silicagel_rH | silicagel_dew | board_C | board_rH | board_dew | ext_C | ext_rH | ext_dew | heater_C | aux_C
74 | SM_STATE | _state_regenerate | Init | ambient_Fan | silicagel_C | silicagel_rH | silicagel_dew | board_C | board_rH | board_dew | ext_C | ext_rH | ext_dew | heater_C | aux_C
870 | SENSORS_VALUES | 78 | 0 | 0 | 23.89 | 13.4 | -5.7 | 24.16 | 32.2 | 6.6 | 23.71 | 69.2 | 17.8 | 24.81 | 23.81
2791 | SENSORS_VALUES | 78 | 0 | 0 | 23.86 | 13.5 | -5.7 | 24.16 | 32.2 | 6.6 | 23.75 | 69.2 | 17.8 | 25 | 23.75
4791 | SENSORS_VALUES | 78 | 0 | 0 | 23.86 | 13.4 | -5.7 | 24.18 | 32.2 | 6.6 | 23.75 | 69.2 | 17.8 | 25.44 | 23.75
6791 | SENSORS_VALUES | 78 | 0 | 0 | 23.87 | 13.4 | -5.7 | 24.16 | 32.2 | 6.6 | 23.74 | 69.2 | 17.8 | 26.13 | 23.75
8791 | SENSORS_VALUES | 78 | 0 | 0 | 23.86 | 13.4 | -5.8 | 24.18 | 32.2 | 6.6 | 23.72 | 69.2 | 17.8 | 26.88 | 23.75
10791 | SENSORS_VALUES | 78 | 0 | 0 | 23.87 | 13.3 | -5.8 | 24.19 | 32.1 | 6.6 | 23.72 | 69.2 | 17.8 | 27.81 | 23.75
12791 | SENSORS_VALUES | 78 | 0 | 0 | 23.89 | 13.3 | -5.9 | 24.22 | 32.2 | 6.6 | 23.75 | 69.2 | 17.8 | 28.75 | 23.81
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

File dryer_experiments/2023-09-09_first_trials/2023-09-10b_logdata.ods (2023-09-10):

1 | x | heater_heater | silicagel_Fan | ambient_Fan | silicagel_C | silicagel_rH | silicagel_dew | board_C | board_rH | board_dew | ext_C | ext_rH | ext_dew | heater_C | aux_C
80791 | SENSORS_VALUES | 78 | 0 | 1 | 39.72 | 46.3 | 26.1 | 28.87 | 57.9 | 19.8 | 25.94 | 65.3 | 19 | 85.44 | 26.75
90792 | SENSORS_VALUES | 78 | 0 | 1 | 40.02 | 46.3 | 26.3 | 28.89 | 57.9 | 19.8 | 25.96 | 65.7 | 19.1 | 86 | 26.75
100791 | SENSORS_VALUES | 78 | 0 | 1 | 40.33 | 46.3 | 26.6 | 28.94 | 57.9 | 19.9 | 25.94 | 65.3 | 19 | 86.56 | 26.75
110792 | SENSORS_VALUES | 78 | 0 | 1 | 40.64 | 46.2 | 26.9 | 28.95 | 57.9 | 19.9 | 25.95 | 65.4 | 19 | 87 | 26.75
120791 | SENSORS_VALUES | 78 | 0 | 1 | 40.95 | 46.1 | 27.1 | 29 | 58 | 19.9 | 25.96 | 65.5 | 19 | 87.38 | 26.75
130792 | SENSORS_VALUES | 78 | 0 | 1 | 41.23 | 46 | 27.3 | 29.03 | 58 | 20 | 25.95 | 65.4 | 19 | 87.81 | 26.75
140792 | SENSORS_VALUES | 78 | 0 | 1 | 41.54 | 45.9 | 27.6 | 29.04 | 58 | 20 | 25.96 | 65.4 | 19 | 88.13 | 26.75
150791 | SENSORS_VALUES | 78 | 0 | 1 | 41.77 | 45.8 | 27.7 | 29.08 | 58.1 | 20.1 | 25.96 | 65.4 | 19 | 88.44 | 26.81
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

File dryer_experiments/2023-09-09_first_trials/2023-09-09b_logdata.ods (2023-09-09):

 |  | heater_heater | silicagel_Fan | ambient_Fan | silicagel_C | silicagel_rH | silicagel_dew | board_C | board_rH | board_dew | ext_C | ext_rH | ext_dew | board_C | aux_C
136811 | SENSORS_VALUES | 200 | 0 | 1 | 35.28 | 52.5 | 24.1 | 28.7 | 75.8 | 24 | 25.44 | 66.8 | 18.9 | 71.88 | 26.5
138801 | SENSORS_VALUES | 200 | 0 | 1 | 35.28 | 52.6 | 24.2 | 28.66 | 75.7 | 24 | 25.45 | 66.8 | 18.9 | 72.13 | 26.5
140805 | SENSORS_VALUES | 200 | 0 | 1 | 35.29 | 52.7 | 24.2 | 28.67 | 75.7 | 24 | 25.47 | 66.7 | 18.9 | 72.31 | 26.5
142801 | SENSORS_VALUES | 200 | 0 | 1 | 35.29 | 52.8 | 24.2 | 28.69 | 75.6 | 24 | 25.45 | 66.7 | 18.9 | 72.56 | 26.5
144801 | SENSORS_VALUES | 200 | 0 | 1 | 35.26 | 52.9 | 24.3 | 28.69 | 75.6 | 24 | 25.45 | 66.7 | 18.9 | 72.81 | 26.5
146801 | SENSORS_VALUES | 200 | 0 | 1 | 35.28 | 53 | 24.3 | 28.69 | 75.6 | 24 | 25.45 | 66.8 | 18.9 | 73 | 26.5
148801 | SENSORS_VALUES | 200 | 0 | 1 | 35.28 | 53.1 | 24.3 | 28.69 | 75.5 | 24 | 25.47 | 66.8 | 18.9 | 73.25 | 26.5
150805 | SENSORS_VALUES | 200 | 0 | 1 | 35.25 | 53.3 | 24.3 | 28.69 | 75.5 | 24 | 25.48 | 66.8 | 18.9 | 73.5 | 26.5
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

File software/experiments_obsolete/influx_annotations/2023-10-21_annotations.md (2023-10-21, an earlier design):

2023-10-21_annotations_a.json

```flux
from(bucket: "filament_dryer")
  |> range(start: 2023-10-21T11:40:41Z, stop: 2023-10-21T11:40:59Z)
  |> filter(fn: (r) => r["_measurement"] == "dryer_prototype_v1.0_1")
```

```json
      {
        "name": "dryer_prototype_v1.0_1",
        "refId": "A",
        "fields": [
          {
            "name": "Time",
...
            "values": [
              1697888453551
            ],
          },
          {
            "name": "text",
            "type": "string",
            "typeInfo": {
              "frame": "string",
              "nullable": true
            },
            "labels": {
              "event": "annotation",
              "room": "B15",
              "setup": "zeus",
              "topic": "forward2influxdb"
            },
            "config": {},
            "values": [
              "Why: User Button: Forward to next state"
            ],
            "entities": {},
            "state": null
          }
        ],
        "length": 1
      },
```

```json
    {
      "name": "dryer_prototype_v1.0_1",
      "refId": "A",
      "fields": [
        {
          "name": "Time",
          "type": "time",
...
          "values": [
            1697888453551
          ],
        },
        {
          "name": "severity",
          "type": "string",
          "typeInfo": {
            "frame": "string",
            "nullable": true
          },
          "labels": {
            "event": "annotation",
            "room": "B15",
            "setup": "zeus",
            "topic": "forward2influxdb"
          },
          "config": {},
          "values": [
            "INFO"
          ],
          "entities": {},
          "state": null
        }
      ],
      "length": 1
    },
  ```
2023-10-21_annotations_b.json

```flux
from(bucket: "filament_dryer")
  |> range(start: 2023-10-21T11:40:41Z, stop: 2023-10-21T11:40:59Z)
```

```json
...
```

```
import "types"

from(bucket: "filament_dryer")
  |> range(start: v.timeRangeStart, stop:v.timeRangeStop)
  |> filter(fn: (r) => r._measurement == "${filament_dryer}")
  |> filter(fn: (r) => r._field != "statemachine")
//  |> filter(fn: (r) => r.event != "annotation")
//  |> filter(fn: (r) => r._field != "statemachine")
//  |> filter(fn: (r) => not types.isType(v: r._value, type: "string"))
//  |> filter(fn: (r) => types.isNumeric(v: r._value))
//  |> filter(fn: (r) => types.isNumeric(v: r._value))
//  |> aggregateWindow(every: 300s, fn: mean, createEmpty: false)
//  |> yield(name: "mean")
```

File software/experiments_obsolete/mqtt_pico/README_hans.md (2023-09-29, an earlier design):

# MQTT

## Links
https://www.youtube.com/watch?v=vehHapPX_E8
https://www.youtube.com/watch?v=f7ws9pfLmJc
https://www.influxdata.com/integration/mqtt-telegraf-consumer/
https://github.com/influxdata/telegraf/tree/master/plugins/parsers/json_v2
http://mqtt-explorer.com/

## umqtt.simple
https://github.com/donskytech/micropython-raspberry-pi-pico/blob/main/umqtt.simple/main.py

## Topic parsing
https://www.donskytech.com/umqtt-simple-micropython-tutorial/#htoc-h
https://www.influxdata.com/blog/mqtt-topic-payload-parsing-telegraf/

## json_v2
https://www.mikrocontroller.net/topic/545947

# Vorschlag Peter

Via mqtt einen String schicken an Topic `influx`.

Der String hat dieses Format:

* https://github.com/nanophysics/pico_nano_monitor/blob/main/utils.py
* # payload = f"airSensor,sensorId=A0100,station=Harbor humidity=35.0658,temperature=37.2" 

* https://github.com/nanophysics/pico_nano_monitor/blob/influxdb_structure.py

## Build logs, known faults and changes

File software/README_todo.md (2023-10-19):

DONE: silicagel_fan -> filament_fan
DONE: filament_dew -> filament_dew_C
DONE: Button funktioniert nicht.
TODO: Watchdog
DONE: Uptime
NOT: Heater Power: Modulate

https://github.com/nanophysics/pico_nano_monitor/blob/main/utils.py

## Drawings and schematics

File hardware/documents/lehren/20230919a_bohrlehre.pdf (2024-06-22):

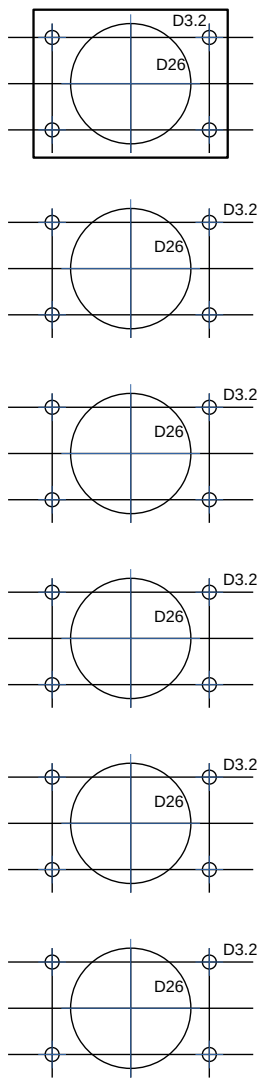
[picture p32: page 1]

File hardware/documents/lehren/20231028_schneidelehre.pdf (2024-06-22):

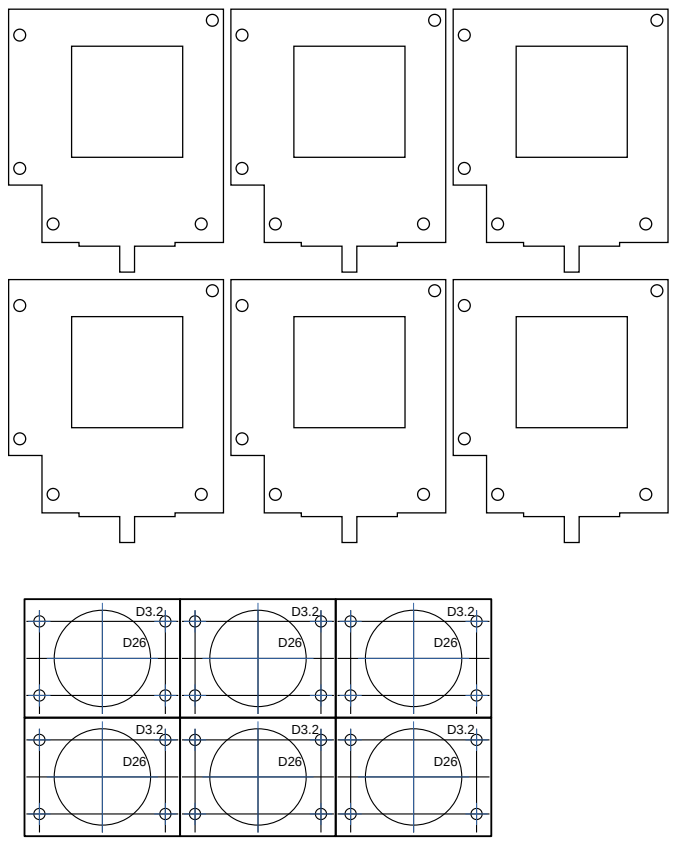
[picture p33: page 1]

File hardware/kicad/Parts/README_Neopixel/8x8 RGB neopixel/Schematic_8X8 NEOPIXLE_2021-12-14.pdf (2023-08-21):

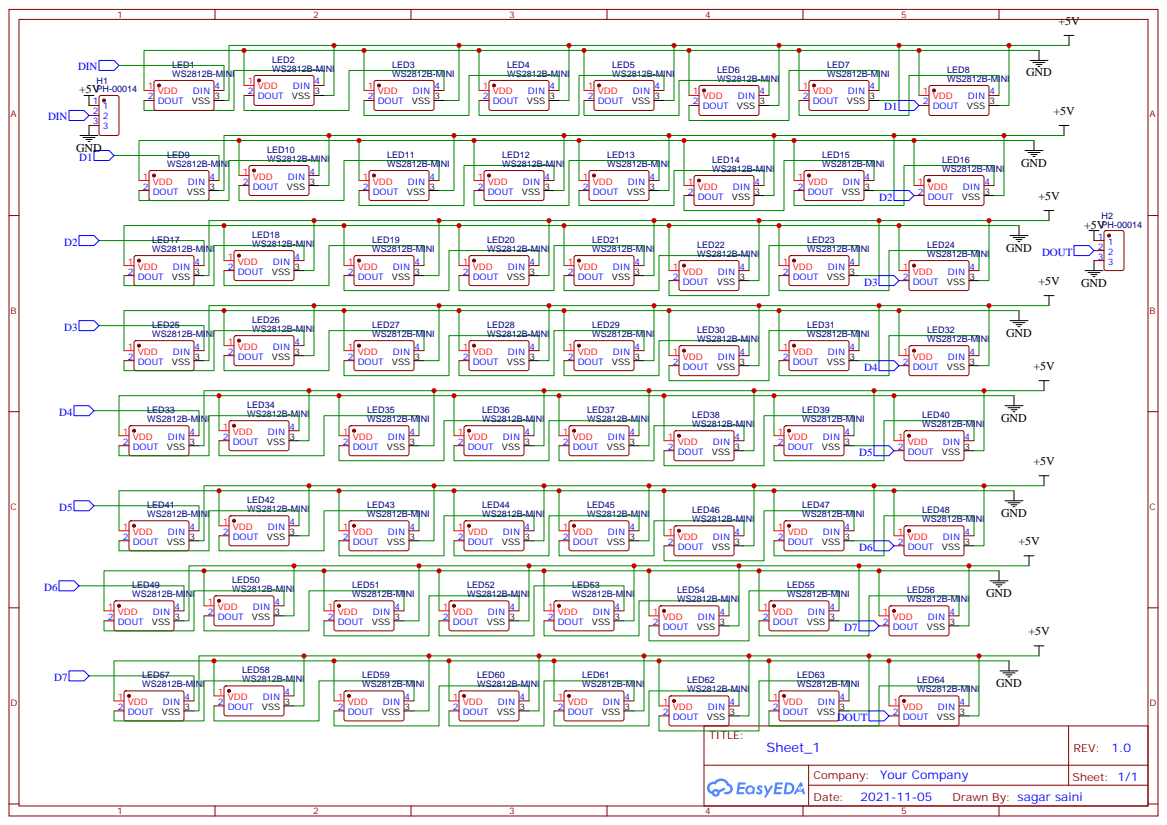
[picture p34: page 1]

Drawn By: sagar saini

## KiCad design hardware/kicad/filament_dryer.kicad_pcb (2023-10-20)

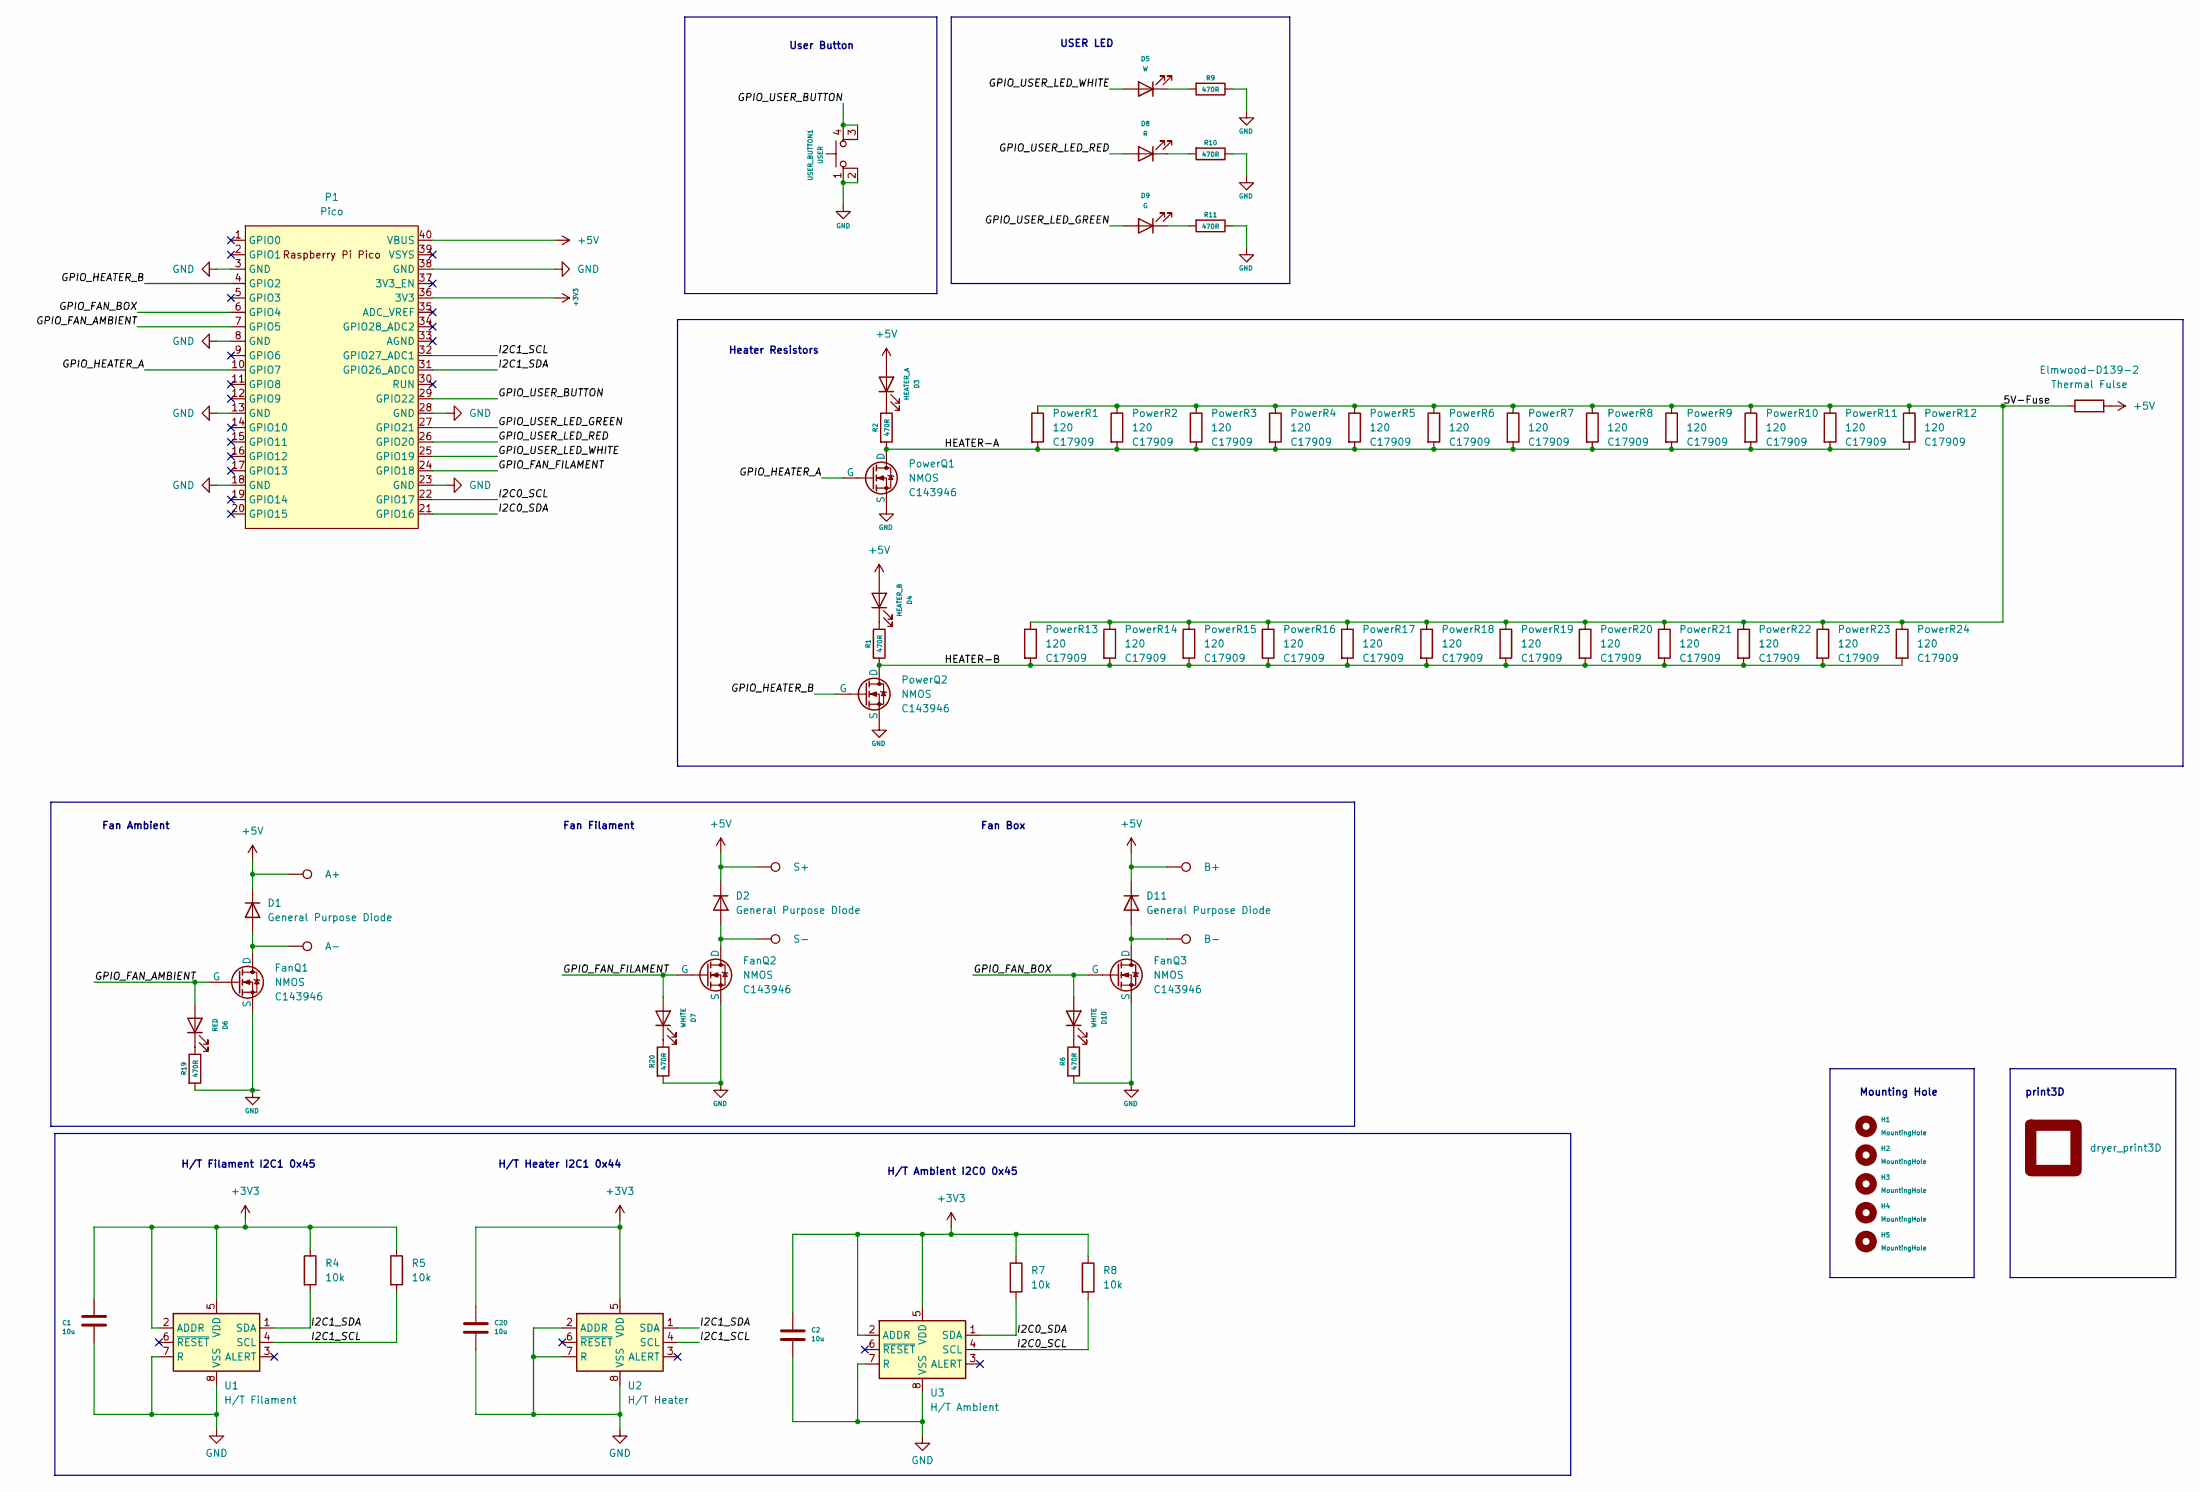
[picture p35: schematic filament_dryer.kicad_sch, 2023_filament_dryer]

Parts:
C1, C2: 10u; C_0603_1608Metric; JLC C96446
C20: 10u; C_0603_1608Metric
D1, D2, D11: General Purpose Diode; D_SMA; JLC Part C95872
D3: HEATER_A; LED_0603_1608Metric; JLC C2286
D4: HEATER_B; LED_0603_1608Metric; JLC C2286
D5: W; LED_0603_1608Metric; JLC C2290
D6: RED; LED_0603_1608Metric; JLC C2286
D7, D10: WHITE; LED_0603_1608Metric; JLC C2290
D8: R; LED_0603_1608Metric; JLC C2286
D9: G; LED_0603_1608Metric; JLC C2297
Elmwood-D139-2: Thermal Fulse; Thermal Fuse (R_Axial_Power_L25.0mm_W6.4mm_P27.94mm)
FanQ1, FanQ2, FanQ3: NMOS; SOT-23; JLC Part C143946
H1, H2, H3, H4, H5: MountingHole; MountingHole_3.2mm_M3
P1: Pico; RPi_Pico
PowerQ1, PowerQ2: NMOS; SOT-23; JLC Part C143946
PowerR1, PowerR2, PowerR3, PowerR4, PowerR5, PowerR6, PowerR7, PowerR8, PowerR9, PowerR10, PowerR11, PowerR12, PowerR13, PowerR14, PowerR15, PowerR16, PowerR17, PowerR18, PowerR19, PowerR20, PowerR21, PowerR22, PowerR23, PowerR24: 120; R_1206_3216Metric; JLC Part C17909
R1, R2, R6, R9, R10, R11, R19, R20: 470R; R_0402_1005Metric_Pad0.72x0.64mm_HandSolder
R4, R5, R7, R8: 10k; R_0402_1005Metric_Pad0.72x0.64mm_HandSolder
TP1: B+; TestPoint_Pad_D3.0mm
TP2: B-; TestPoint_Pad_D3.0mm
TP7: A+; TestPoint_Pad_D3.0mm
TP8: A-; TestPoint_Pad_D3.0mm
TP9: S+; TestPoint_Pad_D3.0mm
TP10: S-; TestPoint_Pad_D3.0mm
U1: H/T Filament; SON50P250X250X90-9T110X180N; JLC C80862
U2: H/T Heater; SON50P250X250X90-9T110X180N; JLC C80862
U3: H/T Ambient; SON50P250X250X90-9T110X180N; JLC C80862
USER_BUTTON1: USER; SW_TS-1187A-B-A-B; JLC C318884
dryer_print3D1: dryer_print3D; dryer_print3d

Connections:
+3V3: C1.1, C2.1, C20.1, P1.36 (3V3), R4.1, R5.1, R7.1, R8.1, U1.2 (ADDR), U1.5 (VDD), U2.5 (VDD), U3.2 (ADDR), U3.5 (VDD)
+5V: D1.1 (K), D2.1 (K), D3.2 (A), D4.2 (A), D11.1 (K), Elmwood-D139-2.2, P1.40 (VBUS), TP1.1, TP7.1, TP9.1
/5V-Fuse: Elmwood-D139-2.1, PowerR1.1, PowerR2.1, PowerR3.1, PowerR4.1, PowerR5.1, PowerR6.1, PowerR7.1, PowerR8.1, PowerR9.1, PowerR10.1, PowerR11.1, PowerR12.1, PowerR13.1, PowerR14.1, PowerR15.1, PowerR16.1, PowerR17.1, PowerR18.1, PowerR19.1, PowerR20.1, PowerR21.1, PowerR22.1, PowerR23.1, PowerR24.1
/GPIO_FAN_AMBIENT: D6.2 (A), FanQ1.1 (G), P1.7 (GPIO5)
/GPIO_FAN_BOX: D10.2 (A), FanQ3.1 (G), P1.6 (GPIO4)
/GPIO_FAN_FILAMENT: D7.2 (A), FanQ2.1 (G), P1.24 (GPIO18)
/GPIO_HEATER_A: P1.10 (GPIO7), PowerQ1.1 (G)
/GPIO_HEATER_B: P1.4 (GPIO2), PowerQ2.1 (G)
/GPIO_USER_BUTTON: P1.29 (GPIO22), USER_BUTTON1.3 (K), USER_BUTTON1.4 (A)
/GPIO_USER_LED_GREEN: D9.2 (A), P1.27 (GPIO21)
/GPIO_USER_LED_RED: D8.2 (A), P1.26 (GPIO20)
/GPIO_USER_LED_WHITE: D5.2 (A), P1.25 (GPIO19)
/HEATER-A: PowerQ1.3 (D), PowerR1.2, PowerR2.2, PowerR3.2, PowerR4.2, PowerR5.2, PowerR6.2, PowerR7.2, PowerR8.2, PowerR9.2, PowerR10.2, PowerR11.2, PowerR12.2, R2.2
/HEATER-B: PowerQ2.3 (D), PowerR13.2, PowerR14.2, PowerR15.2, PowerR16.2, PowerR17.2, PowerR18.2, PowerR19.2, PowerR20.2, PowerR21.2, PowerR22.2, PowerR23.2, PowerR24.2, R1.2
/I2C0_SCL: P1.22 (GPIO17), R8.2, U3.4 (SCL)
/I2C0_SDA: P1.21 (GPIO16), R7.2, U3.1 (SDA)
/I2C1_SCL: P1.32 (GPIO27_ADC1), R5.2, U1.4 (SCL), U2.4 (SCL)
/I2C1_SDA: P1.31 (GPIO26_ADC0), R4.2, U1.1 (SDA), U2.1 (SDA)
GND: C1.2, C2.2, C20.2, FanQ1.2 (S), FanQ2.2 (S), FanQ3.2 (S), P1.3 (GND), P1.8 (GND), P1.13 (GND), P1.18 (GND), P1.23 (GND), P1.28 (GND), P1.38 (GND), PowerQ1.2 (S), PowerQ2.2 (S), R6.2, R9.1, R10.1, R11.1, R19.2, R20.2, U1.7 (R), U1.8 (VSS), U1.9 (VSS), U2.2 (ADDR), U2.7 (R), U2.8 (VSS), U2.9 (VSS), U3.7 (R), U3.8 (VSS), U3.9 (VSS), USER_BUTTON1.1, USER_BUTTON1.2
unnamed: D1.2 (A), FanQ1.3 (D), TP8.1
unnamed: D2.2 (A), FanQ2.3 (D), TP10.1
unnamed: D3.1 (K), R2.1
unnamed: D4.1 (K), R1.1
unnamed: D5.1 (K), R9.2
unnamed: D6.1 (K), R19.1
unnamed: D7.1 (K), R20.1
unnamed: D8.1 (K), R10.2
unnamed: D9.1 (K), R11.2
unnamed: D10.1 (K), R6.1
unnamed: D11.2 (A), FanQ3.3 (D), TP2.1

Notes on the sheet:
Mounting Hole
User Button
USER LED
H/T Ambient I2C0 0x45
Fan Filament
Heater Resistors
Fan Box
print3D
Fan Ambient
H/T Heater I2C1 0x44
H/T Filament I2C1 0x45

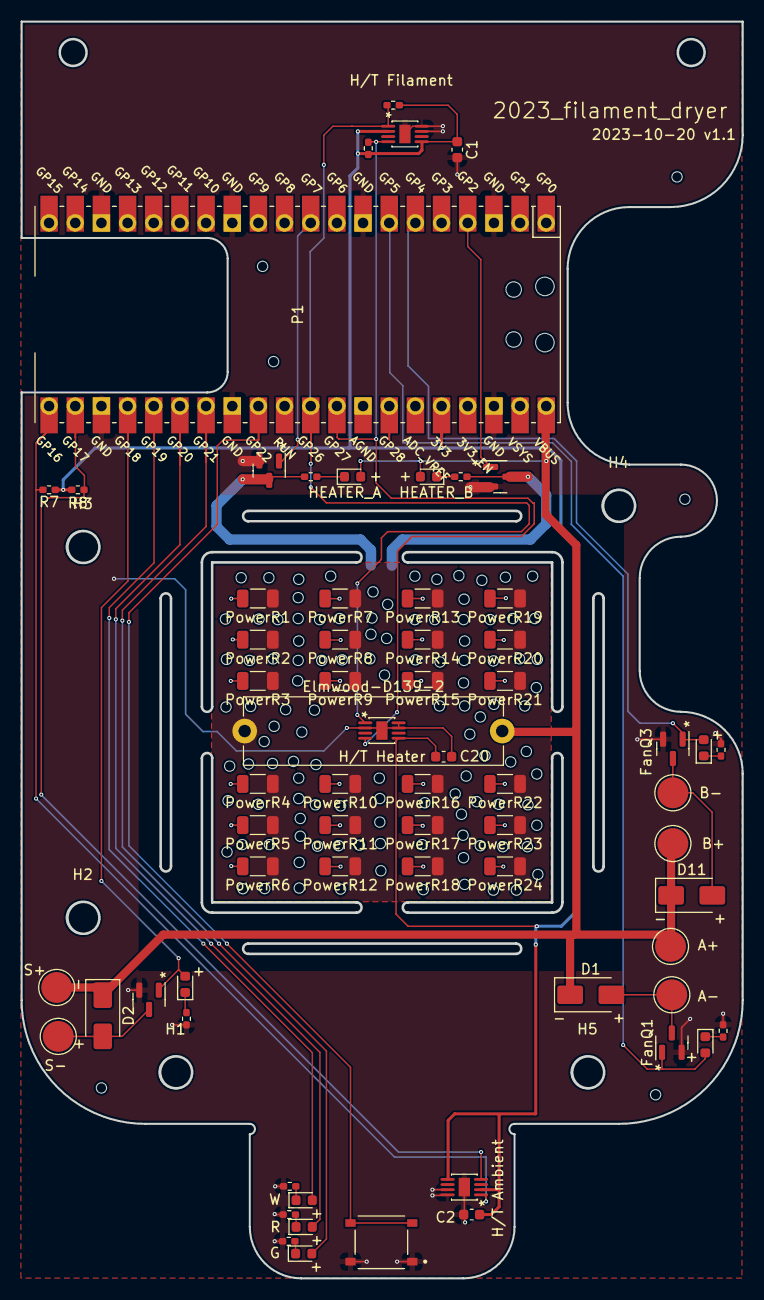
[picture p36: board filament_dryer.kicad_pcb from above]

Board: 2 copper layers, 70.0 x 122.0 mm, 73 parts (0 on the bottom side), 30 nets.

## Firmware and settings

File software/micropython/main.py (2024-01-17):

import rp2
import os
import gc
import machine
import micropython
import _thread


micropython.alloc_emergency_exception_buf(100)

import utils_button
import utils_wlan
import utils_constants
import config_secrets
from utils_wdt import wdt
from utils_logstdout import logfile
from utils_log import LogfileTags
from utils_timebase import tb
from mod_hardware import Hardware
from mod_sensoren import Sensoren
from mod_statemachine import Statemachine
from utils_app_package_poll import new_version_available, sw_version
from utils_constants import DIRECTORY_LOGS

ENABLE_APP_PACKAGE_UPDATE = True
ENABLE_WDT = True

boot_cause = {
    machine.PWRON_RESET: "power on",
    machine.WDT_RESET: "watchdog reset",
}.get(machine.reset_cause(), "soft reset")
print(f"Boot cause: {boot_cause} ({machine.reset_cause()})")

hardware = Hardware()

if ENABLE_WDT and (hardware.PIN_GPIO_BUTTON.value() == 1):
    wdt.enable()
    print("To disable the watchdog: Press the user button before power on...")
else:
    print("User button pressed: Watchdog disabled!")
    ENABLE_APP_PACKAGE_UPDATE = False
    wdt.disable()

# hardware.production_test(wdt.feed)
sensoren = Sensoren(hardware=hardware)

sm = Statemachine(hardware=hardware, sensoren=sensoren)
sensoren.sensor_statemachine.set_sm(sm=sm)


class AppPackage:
    def __init__(self):
        self.next_poll_ms = 0

    def poll(self):
        if not ENABLE_APP_PACKAGE_UPDATE:
            return

        if tb.now_ms < self.next_poll_ms:
            return

        self.next_poll_ms += 10 * utils_constants.DURATION_MIN_MS

        # version = "mpy_version/6.1"
        version = "src"
        dict_tar = new_version_available(version, wdt_feed=wdt.feed)

        if dict_tar is not None:
            # Upload late: We will reboot afterwords!
            from utils_app_package_download import download_new_version

            download_new_version(dict_tar, wdt_feed=wdt.feed)


def main_core2(mqtt):
    print("DEBUG: main_core2: started")

    def statechange(old: str, new: str, why: str) -> None:
        mqtt.publish_annotation(
            title=f"Statechange: {old} -> {new}", text=f"Why: {why}"
        )

    sm.statechange_cb = statechange

    def statemachine_cb(msg: str):
        print(f"statemachine_cb: {msg}")
        sm.switch_by_name(msg)

    mqtt.register_callback("statemachine", statemachine_cb)

    # logfile.log(LogfileTags.SENSORS_HEADER, sensoren.sensors.get_header())

    mqtt_first_time_counter = 0
    app_package = AppPackage()
    while True:
        hardware.led_toggle()
        sensoren.measure()
        hardware.led_toggle()

        sm.state()
        hardware.heater.set_board_C(board_C=sensoren.heater_C)

        # logfile.log(LogfileTags.LOG_DEBUG, f"{tb.sleep_done_ms}, {tb.sleep_done_ms}")
        logfile.log(
            LogfileTags.SENSORS_VALUES,
            sensoren.sensors.get_values(sensoren.stdout_measurements),
            stdout=False,
        )

        # Send two annotations within 20s
        if mqtt_first_time_counter == 1:
            if mqtt.publish_annotation(
                title="Software version",
                text=sw_version(),
            ):
                mqtt_first_time_counter += 1
        if mqtt_first_time_counter == 0:
            if mqtt.publish_annotation(
                title=f"Boot due to {boot_cause}",
                text=f"serial {config_secrets.HW_SERIAL}, {config_secrets.HW_VERSION}, {wlan.ip_address}",
            ):
                mqtt_first_time_counter += 1

        mqtt.publish(fields=sensoren.sensors.get_mqtt_fields(), tags={})

        if wlan.got_ip_address:
            app_package.poll()

        gc.collect()
        tb.sleep()


def pressed(duration_ms: int) -> None:
    sm.set_forward_to_next_state()


def long_pressed(timer) -> None:
    # Hard reset micropython
    machine.reset()


utils_button.Button(
    hardware.PIN_GPIO_BUTTON,
    pressed_cb=pressed,
    cb_long_press=long_pressed,
    long_press_ms=2000,
    invers=True,
)


def thread():
    _thread.start_new_thread(main_core2, ())


def values():
    print(sensoren.sensors.get_header(measurements=sensoren.stdout_measurements))
    print(sensoren.sensors.get_values(measurements=sensoren.stdout_measurements))


def valuesall():
    print(sensoren.sensors.get_header())
    print(sensoren.sensors.get_values())


def power_off():
    wlan.power_off()


def df():  # Disk Free
    print("*** Garbage")
    print(
        f"Allocated/Free {gc.mem_alloc()/1000.0:0.3f}/{gc.mem_free()/1000.0:0.3f} kBytes"
    )
    gc.collect()
    print(
        f"Allocated/Free {gc.mem_alloc()/1000.0:0.3f}/{gc.mem_free()/1000.0:0.3f} kBytes"
    )

    print("*** Filesystem")
    logfile.flush()
    (
        f_bsize,
        f_frsize,
        f_blocks,
        f_bfree,
        f_bavail,
        f_files,
        f_ffree,
        f_favail,
        f_flag,
        f_namemax,
    ) = os.statvfs(DIRECTORY_LOGS)
    print(f"File system size total:  {f_blocks*f_frsize/1024.0} kBytes")
    print(f"File system size free:  {f_bavail*f_bsize/1024.0} kBytes")
    print(f"File system inodes free:  {f_favail}/{f_ffree} inodes")

    # print("*** Logfiles")
    # for name, type, inode, size in os.ilistdir("logs"):
    #     print(f"{DIRECTORY_LOGS}/{name}: {size} bytes")


def format():  # Reformat
    hardware.heater.set_power(False)

    # https://www.i-programmer.info/programming/hardware/16334-raspberry-pi-pico-file-system-a-sd-card-reader.html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
    flash = rp2.Flash()
    os.umount("/")
    os.VfsLfs2.mkfs(flash)
    os.mount(flash, "/")
    machine.soft_reset()


def smp():
    print(sm.state_name)


def smx(new_state: str):
    sm.switch_by_name(new_state)


wlan = utils_wlan.WLAN()
wlan.register_wdt_feed_cb(wdt.feed)
# Make sure, the connection before the reboot is dropped.
wlan.power_off()
wlan.connect()
mqtt = utils_wlan.MQTT(wlan)

if True:
    main_core2(mqtt)
else:
    _thread.start_new_thread(main_core2, (mqtt,))

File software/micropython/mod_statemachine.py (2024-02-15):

import time
import config

from utils_logstdout import logfile
from utils_timebase import tb
from utils_log import LogfileTags

try:
    from typing import TYPE_CHECKING

    if TYPE_CHECKING:
        from mod_hardware import Hardware
        from mod_sensoren import Sensoren
except ImportError:
    pass

WHY_FORWARD = "User Button: Forward to next state"


class Statemachine:
    PREFIX_STATE = "_state_"
    PREFIX_ENTRY = "_entry_"

    def __init__(self, hardware: Hardware, sensoren: Sensoren):
        self._hw = hardware
        self._sensoren = sensoren

        self._regenerate_last_fanon_ms = time.ticks_ms()
        self._dryfan_list_abs_g_kg = []
        self._dryfan_next_ms = time.ticks_ms()
        self._forward_to_next_state = False
        self.statechange_cb = lambda state, new_state, why: state
        # Attention: The three following lines have to match the same state
        self.state_name = "cooldown"
        self.state = self._state_cooldown
        self._entry_cooldown()

    def set_forward_to_next_state(self) -> None:
        self._forward_to_next_state = True
        self.state()

    @property
    def forward_to_next_state(self) -> bool:
        if self._forward_to_next_state:
            self._forward_to_next_state = False
            return True
        return False

    def switch_by_name(self, new_state: str) -> None:
        state_name = f"_state_{new_state}"
        print(f"state_name: '{state_name}'")
        try:
            state_func = getattr(self, state_name)
        except AttributeError as e:
            print(f"WARNING: Unexisting state '{state_name}'!")
            return
        self._switch(state_func, "MQTT intervention")

    def _switch(self, new_state, why: str) -> None:
        assert new_state.__name__.startswith(self.PREFIX_STATE)
        new_state_name = new_state.__name__.replace(self.PREFIX_STATE, "")
        if self.state_name == new_state_name:
            return
        msg = f"'{self.state_name}' -> '{new_state_name}' {why}"
        logfile.log(LogfileTags.SM_STATE, msg, stdout=True)
        self.statechange_cb(self.state_name, new_state_name, why)
        self.state_name = new_state_name
        self.state = new_state

        new_entry_name = self.PREFIX_ENTRY + new_state_name
        f_entry = getattr(self, new_entry_name)
        f_entry()

    # State: OFF
    def _entry_off(self) -> None:
        self._hw.PIN_GPIO_FAN_AMBIENT.off()
        self._hw.PIN_GPIO_FAN_FILAMENT.off()
        self._hw.PIN_GPIO_FAN_BOX.off()
        self._hw.heater.set_power(False)

        self._hw.PIN_GPIO_LED_GREEN.value(1)
        self._hw.PIN_GPIO_LED_RED.value(1)
        self._hw.PIN_GPIO_LED_WHITE.value(1)

    def _state_off(self) -> None:
        if self.forward_to_next_state:
            self._switch(self._state_regenerate, WHY_FORWARD)

    # State: REGENERATE
    def _entry_regenerate(self) -> None:
        self._regenerate_last_fanon_ms = time.ticks_ms()
        self._hw.PIN_GPIO_FAN_AMBIENT.off()
        self._hw.PIN_GPIO_FAN_FILAMENT.off()
        self._hw.PIN_GPIO_FAN_BOX.off()

        self._hw.PIN_GPIO_LED_GREEN.value(0)
        self._hw.PIN_GPIO_LED_RED.value(1)
        self._hw.PIN_GPIO_LED_WHITE.value(0)

    def _state_regenerate(self) -> None:
        if self.forward_to_next_state:
            self._switch(self._state_cooldown, WHY_FORWARD)
            return

        # Controller for the fan
        diff_abs_g_kg = self._sensoren.heater_abs_g_kg - self._sensoren.ambient_abs_g_kg
        fan_on = (
            diff_abs_g_kg > config.SM_REGENERATE_DIFF_ABS_G_KG
            or self._sensoren.heater_dew_C > self._sensoren.ambient_C - 4.0
        )
        self._hw.PIN_GPIO_FAN_AMBIENT.value(fan_on)

        # Do heat if humidity in heater is not to high
        heat_power_on = self._sensoren.heater_dew_C < self._sensoren.ambient_C + 4.0
        self._hw.heater.set_power(heat_power_on)

        if fan_on:
            self._regenerate_last_fanon_ms = time.ticks_ms()
            return

        # Do state change if fan was off for a 'long' time.
        if self._sensoren.heater_C < config.SM_REGENERATE_HOT_C:
            self._regenerate_last_fanon_ms = time.ticks_ms()
            return

        duration_fan_off_ms = time.ticks_diff(
            time.ticks_ms(), self._regenerate_last_fanon_ms
        )
        assert duration_fan_off_ms >= 0
        if duration_fan_off_ms > config.SM_REGENERATE_NOFAN_MS:
            why = f"duration_fan_off_ms {duration_fan_off_ms}ms > SM_REGENERATE_NOFAN_MS {config.SM_REGENERATE_NOFAN_MS}ms"
            self._switch(self._state_cooldown, why)

    # State: COOL DOWN
    def _entry_cooldown(self) -> None:
        self._hw.PIN_GPIO_FAN_FILAMENT.off()
        self._hw.PIN_GPIO_FAN_BOX.off()
        self._hw.PIN_GPIO_FAN_AMBIENT.off()
        self._hw.heater.set_power(False)

        self._hw.PIN_GPIO_LED_GREEN.value(0)
        self._hw.PIN_GPIO_LED_RED.value(1)
        self._hw.PIN_GPIO_LED_WHITE.value(1)

    def _state_cooldown(self) -> None:
        if self.forward_to_next_state:
            self._switch(self._state_dryfan, WHY_FORWARD)
            return

        heater_C = self._sensoren.heater_C
        if heater_C < config.SM_COOLDOWN_TEMPERATURE_HEATER_C:
            self._switch(
                self._state_dryfan,
                f"heater_C {heater_C:0.1f}C < SM_COOLDOWN_TEMPERATURE_HEATER_C {config.SM_COOLDOWN_TEMPERATURE_HEATER_C:0.1f}C",
            )

    # State: DRY FAN
    def _entry_dryfan(self) -> None:
        self._hw.PIN_GPIO_FAN_FILAMENT.on()
        self._hw.PIN_GPIO_FAN_BOX.on()
        self._hw.PIN_GPIO_FAN_AMBIENT.off()
        self._hw.heater.set_power(False)
        self._dryfan_list_abs_g_kg = []
        self._dryfan_next_ms = time.ticks_ms()

        self._hw.PIN_GPIO_LED_GREEN.value(0)
        self._hw.PIN_GPIO_LED_RED.value(0)
        self._hw.PIN_GPIO_LED_WHITE.value(1)

    def _state_dryfan(self) -> None:
        if self.forward_to_next_state:
            self._switch(self._state_drywait, WHY_FORWARD)
            return

        diff_ms = time.ticks_diff(self._dryfan_next_ms, time.ticks_ms())
        if diff_ms < 0:
            logfile.log(
                LogfileTags.LOG_INFO,
                f"len={len(self._dryfan_list_abs_g_kg)}, append({self._sensoren.filament_abs_g_kg})",
                stdout=True,
            )
            self._dryfan_next_ms = time.ticks_add(
                self._dryfan_next_ms, config.SM_DRYFAN_NEXT_MS
            )
            self._dryfan_list_abs_g_kg.insert(0, self._sensoren.filament_abs_g_kg)
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

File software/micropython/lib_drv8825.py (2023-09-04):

from machine import Pin,
import rp2

class DRV8825:
    """
        https://how2electronics.com/control-stepper-motor-with-drv8825-raspberry-pi-pico/
        
        This statemachine sends 'count' pulses.
        Pulse length is 'pulse_length_us'.
        The statemachine runs at 10MHz
        The pulse takes 10 PIO-instructions
        Therefore 'pulse_length_us' is in micorsecondes (10MHz/10)
    """
    def __init__(self, id: int, pin: Pin):
        assert 0 <= id < 8

        @rp2.asm_pio(set_init=rp2.PIO.OUT_LOW)
        def pulses():
            # x=pulses: how many pulses to send
            pull()
            mov(x, osr)
            
            # y=pulse_length_us: duration of one period
            # Store it in 'isr'. Later, we will assign it to y
            pull()
            mov(isr, osr)

            # Outer loop: pulses
            label("pulses_loop")

            # Positive pulse: 5 instructions
            mov(y, isr)
            set(pins, 1)
            label("pulse_positive")
            jmp(y_dec, "pulse_positive") [4]
            
            # Negative pulse: 5 instructions
            mov(y, isr)
            set(pins, 0)
            label("pulse_negative")
            jmp(y_dec, "pulse_negative") [4]
            
            # Outer loop: pulses
            jmp(x_dec, "pulses_loop")
            
            # Done. This will unblock 'sm.get()'
            push(noblock)


        # state machine 0, running at 10MHz
        self.sm = rp2.StateMachine(id, pulses, freq=10_000_000, set_base=pin)
        
    def send_pulses(self, pulses:int, pulse_length_us = 1_000_000):
        # Empty fifo
        while self.sm.rx_fifo() > 0:
            self.sm.pull()
        self.sm.active(1)
        self.sm.put(pulses-1)
        self.sm.put(pulse_length_us)
        
    def wait(self, blocking=True) -> bool:
        """
        If blocking is True:
           return True
        If blocking is False:
           return False # If still in progress
        return True # If done
        """
        if not blocking:
            if self.sm.rx_fifo() == 0:
                return False
        self.sm.get()
        return True

def main():
    d = DRV8825(id=0, pin=Pin(25, Pin.OUT))
    d.send_pulses(3)
    print("wait() before")
    d.wait()
    print("wait() after")

if __name__ == "__main__":
    main()

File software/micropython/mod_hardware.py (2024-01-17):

from machine import Pin, I2C
import time

import config


class Heater:
    def __init__(self, hardware: "Hardware"):
        self._power = False
        self._board_C = 0.0
        self._hardware = hardware
        self.write_power()

    @property
    def power_controlled(self) -> bool:
        if self._board_C > config.HEATER_BOARD_MAX_C:
            return False
        return self._power

    def set_power(self, power: bool):
        self._power = power

        self.write_power()

    def set_board_C(self, board_C: int):
        self._board_C = board_C

        self.write_power()

    def write_power(self) -> None:
        power = self.power_controlled

        self._hardware.PIN_GPIO_HEATER_A.value(power)
        self._hardware.PIN_GPIO_HEATER_B.value(power)


class Hardware:
    def __init__(self):
        self.PIN_GPIO_BUTTON = Pin("GPIO22", mode=Pin.IN, pull=Pin.PULL_UP)
        self.PIN_GPIO_LED_GREEN = Pin("GPIO21", mode=Pin.OUT, value=0)
        self.PIN_GPIO_LED_RED = Pin("GPIO20", mode=Pin.OUT, value=0)
        self.PIN_GPIO_LED_WHITE = Pin("GPIO19", mode=Pin.OUT, value=0)

        self.PIN_GPIO_HEATER_A = Pin("GPIO7", mode=Pin.OUT, value=0)
        self.PIN_GPIO_HEATER_B = Pin("GPIO2", mode=Pin.OUT, value=0)

        self.PIN_GPIO_FAN_AMBIENT = Pin("GPIO5", mode=Pin.OUT, value=0)  # vorher 0
        self.PIN_GPIO_FAN_FILAMENT = Pin("GPIO18", mode=Pin.OUT, value=0)
        self.PIN_GPIO_FAN_BOX = Pin("GPIO4", mode=Pin.OUT, value=0)

        self.i2c0 = I2C(id=0, scl=Pin("GPIO17"), sda=Pin("GPIO16"), freq=400000)
        self.i2c1 = I2C(id=1, scl=Pin("GPIO27"), sda=Pin("GPIO26"), freq=400000)
        self.heater = Heater(self)

    def led_toggle(self) -> None:
        self.PIN_GPIO_LED_GREEN.toggle()
        self.PIN_GPIO_LED_RED.toggle()
        self.PIN_GPIO_LED_WHITE.toggle()

    def production_test(self, wdt_feed_cb):
        # Neue prints testen
        while True:
            for name, pin in (
                ("led g", self.PIN_GPIO_LED_GREEN),
                ("led r", self.PIN_GPIO_LED_RED),
                ("led w", self.PIN_GPIO_LED_WHITE),
                ("fan silicagel", self.PIN_GPIO_FAN_FILAMENT),
                ("heater a", self.PIN_GPIO_HEATER_A),
                ("heater b", self.PIN_GPIO_HEATER_B),
                ("fan silicagel", self.PIN_GPIO_FAN_BOX),
                ("fan ambient", self.PIN_GPIO_FAN_AMBIENT),
            ):
                print(name)
                pin.value(1)
                time.sleep(2)
                pin.value(0)
                wdt_feed_cb()

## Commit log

2023-08-12 hardware_kicad v0.5
    [110990030.stp, 114020164.stp, IC57_RP2040.step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]
2023-08-12 Add dryer_print3d footprint and pcb
    [20230812a_filament_dryer_silicagel.FCStd, filament_dryer.kicad_pcb]
2023-08-13 Added new parts
    [filament_dryer.kicad_pcb, filament_dryer.kicad_sch, filament_heater.kicad_sch]
2023-08-13 Some more layout
    [filament_dryer.kicad_pcb, filament_dryer.kicad_sch]
2023-08-19 Update 3d footprint
    [dryer_print3d.dxf, dryer_print3d.step, filament_dryer.kicad_pcb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]
2023-08-20 2023-08-20 review schematics
    [filament_dryer.kicad_pcb, filament_dryer.kicad_sch]
2023-08-20 Removed resistors, add locked zones
    [filament_dryer.kicad_pcb, filament_dryer.kicad_sch]
2023-08-20 Last version with resistors
    [filament_dryer.kicad_pcb]
2023-08-21 Ready for second review
    [BOM_PCB_8X8 NEOPIXLE_2021-12-03.csv, filament_dryer.kicad_pcb, filament_dryer.kicad_sch]
2023-08-21 Remove 4 diodes
    [filament_dryer.kicad_sch]
2023-08-21 After second review
    [filament_dryer.kicad_pcb, filament_dryer.kicad_sch]
2023-08-22 After second review 2
    [filament_dryer.kicad_pcb, filament_dryer.kicad_sch]
2023-08-22 hardware_kicad v0.6
    [bom.csv, designators.csv, filament_dryer.kicad_pcb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]
2023-09-06 Successful test on board v0.6
2023-09-09 first experiments
    [2023-09-09b_logdata.ods, 2023-09-09c_logdata.ods]
2023-09-16 drayer_print_3d -> dryer_print_3d
    [dryer_print3d.dxf, dryer_print3d.step, filament_dryer.kicad_pcb]
2023-09-18 umqtt sample
2023-09-18 schematics ready for review
    [filament_dryer.kicad_pcb, filament_dryer.kicad_sch]
2023-09-19 board outline cleaned up
    [dryer_board_fixed.dxf, dryer_board_fixed_cleaned.dxf, filament_dryer.kicad_pcb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]
2023-09-20 update dxf footprint print3d
    [dryer_print3d_cleaned.dxf, filament_dryer.kicad_pcb]
2023-09-22 Preparation for review
    [filament_dryer.kicad_pcb, filament_dryer.kicad_sch]
2023-09-22 Remove library circuitstate
    [bom.csv, designators.csv, filament_dryer.kicad_pcb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]
2023-09-22 fet renumbered
    [filament_dryer.kicad_pcb, filament_dryer.kicad_sch, positions.csv]
2023-09-30 Strage behaviour when running in thread...
2023-09-30 Status LEDs
2023-10-20 v1.1 PCB
    [bom.csv, designators.csv, dryer_board_fixed_cleaned.dxf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]
2023-11-17 heating only if dewpoint of heater low enough
2024-01-17 Button press while power on: disable watchdog
2024-01-17 Toggle LEDs while measuring the sensors
2024-06-22 Add freecad files. Cleanup directory structure.
    [110990030.stp, 114020164.stp, 20230917p_filament_dryer_silicagel.FCStd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]

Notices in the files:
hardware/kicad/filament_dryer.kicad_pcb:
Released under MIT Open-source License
